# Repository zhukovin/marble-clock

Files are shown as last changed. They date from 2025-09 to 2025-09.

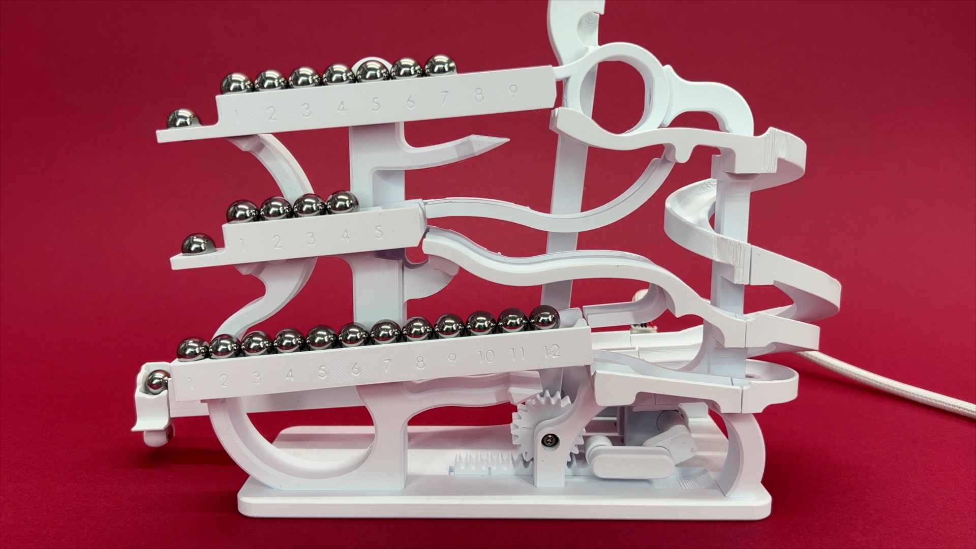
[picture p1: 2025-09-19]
Pictures/How To Assemble the See Saw Clock.jpg

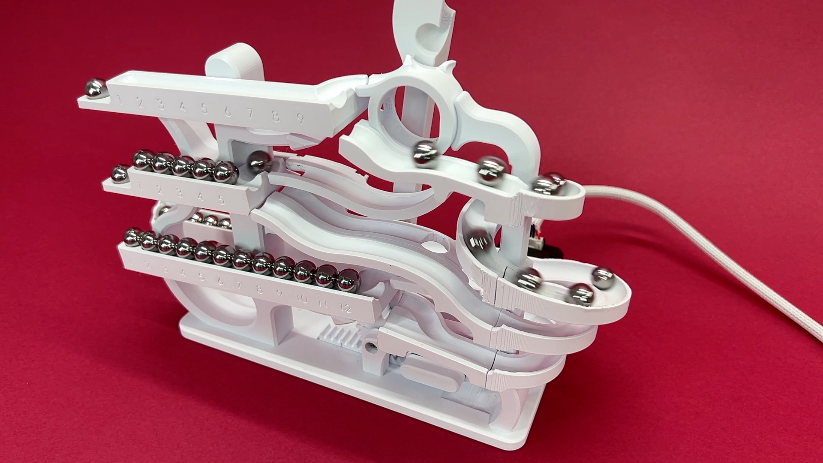
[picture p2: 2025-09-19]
Pictures/How To Assemble the See Saw Clock 4.jpg

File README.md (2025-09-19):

# marble-clock

https://engineezy.com/products/the-tipping-marble-clock

1. 11 3x10x4 bearings: https://a.co/d/4JFZjME
1. M3 Screw Kit: https://a.co/d/3sWPaf0
1. 32 0.5in ball bearings: https://a.co/d/eDzJ6P2
1. Nema 17 Motor: https://a.co/d/04mfYYL
1. 1 GT2 Pulley: https://a.co/d/fuRD2cA
1. A4988 Stepper Motor Driver: https://a.co/d/fOQgJpc
1. Wemos d1 mini ESP8266: https://a.co/d/8dCLFfo
1. Silicone grease: https://a.co/d/iCrpBB1

https://www.youtube.com/watch?v=GmLEBhJY5ks

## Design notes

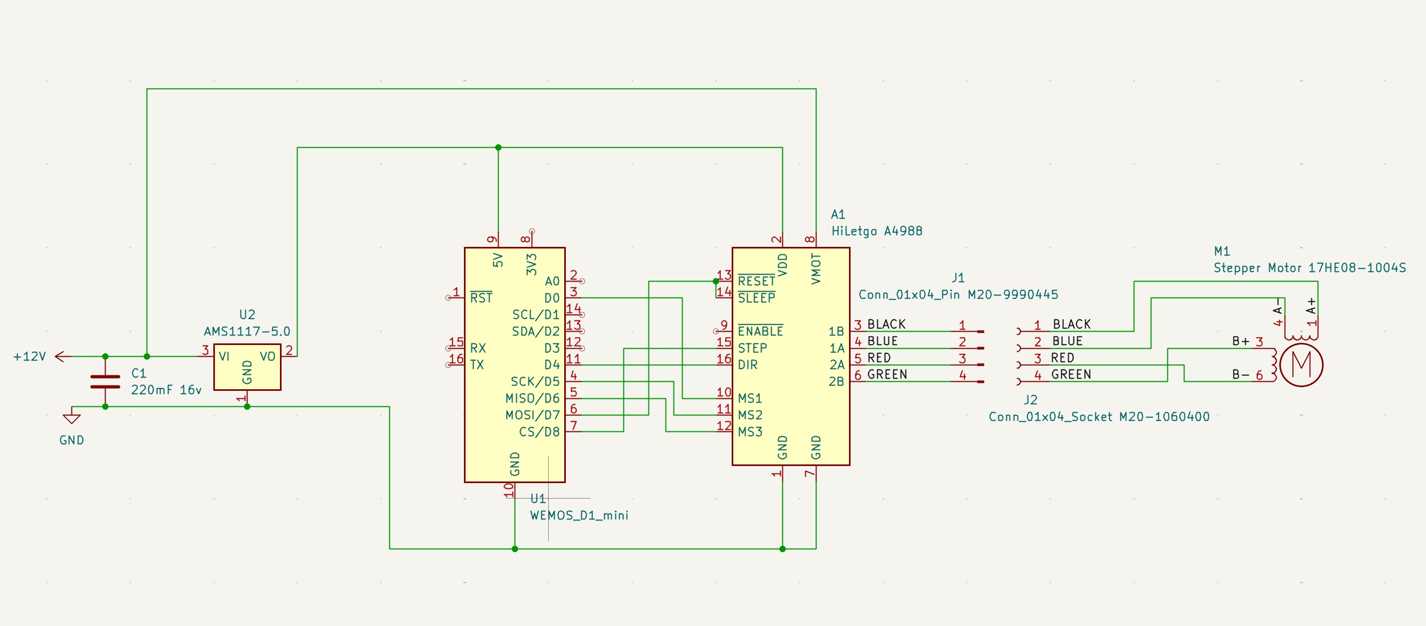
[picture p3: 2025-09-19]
schematic.jpg

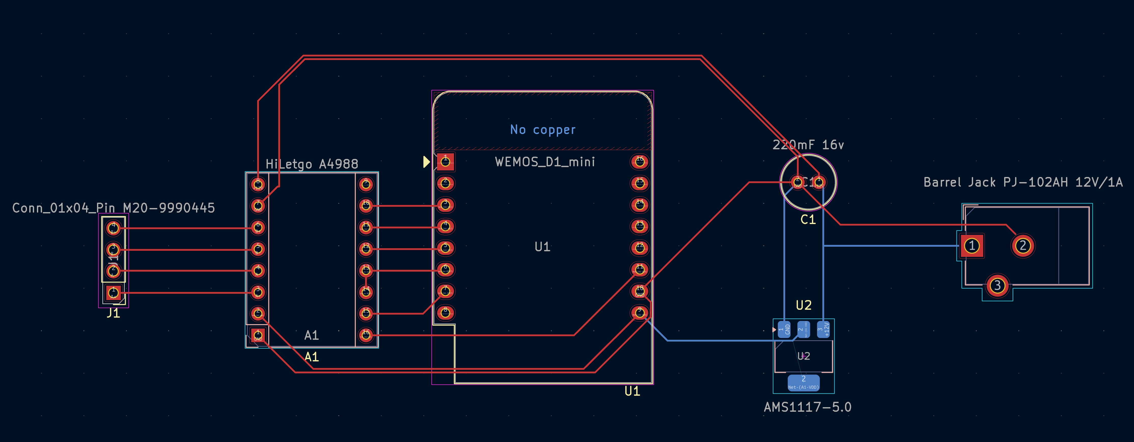
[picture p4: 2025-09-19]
pcb.jpg

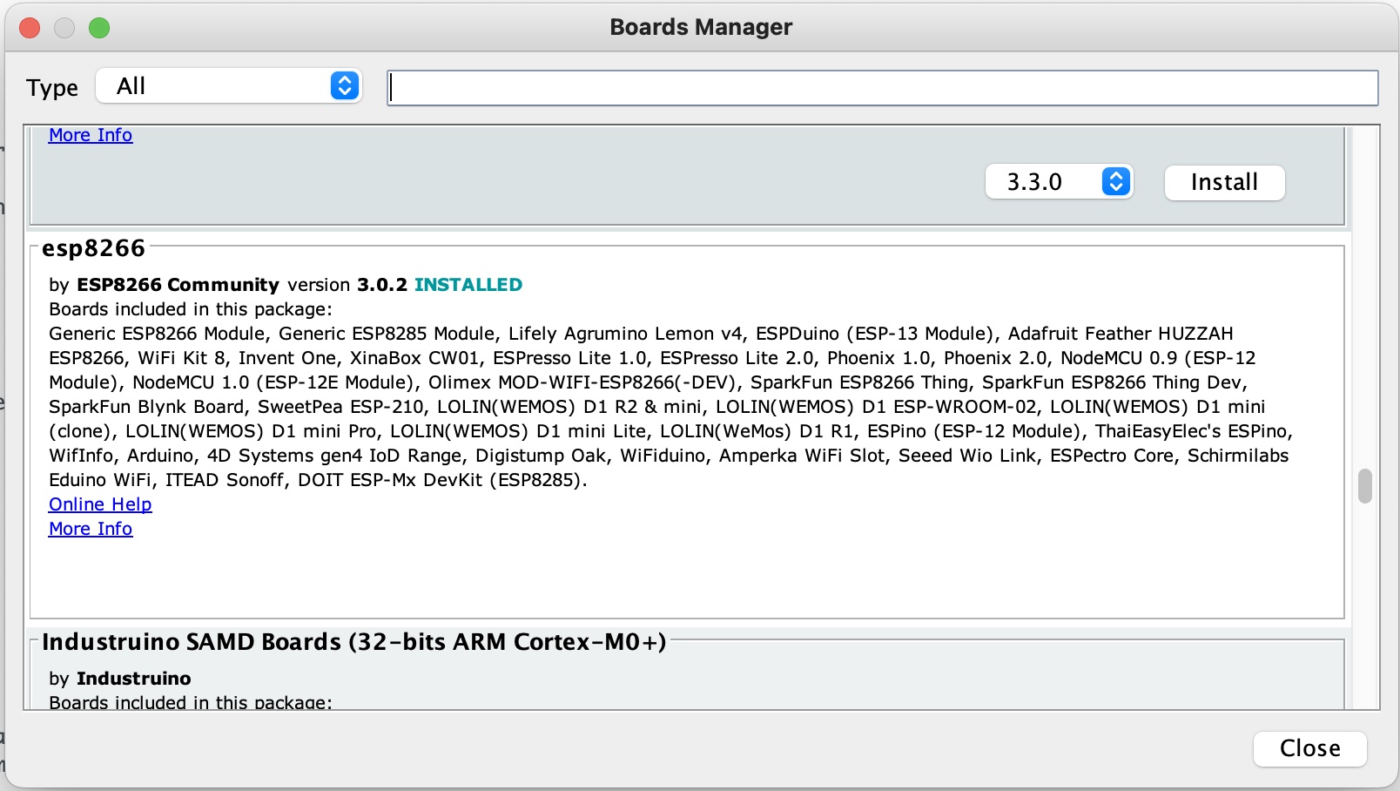
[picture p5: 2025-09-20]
Arduino/Wemos-esp8266-board.jpg

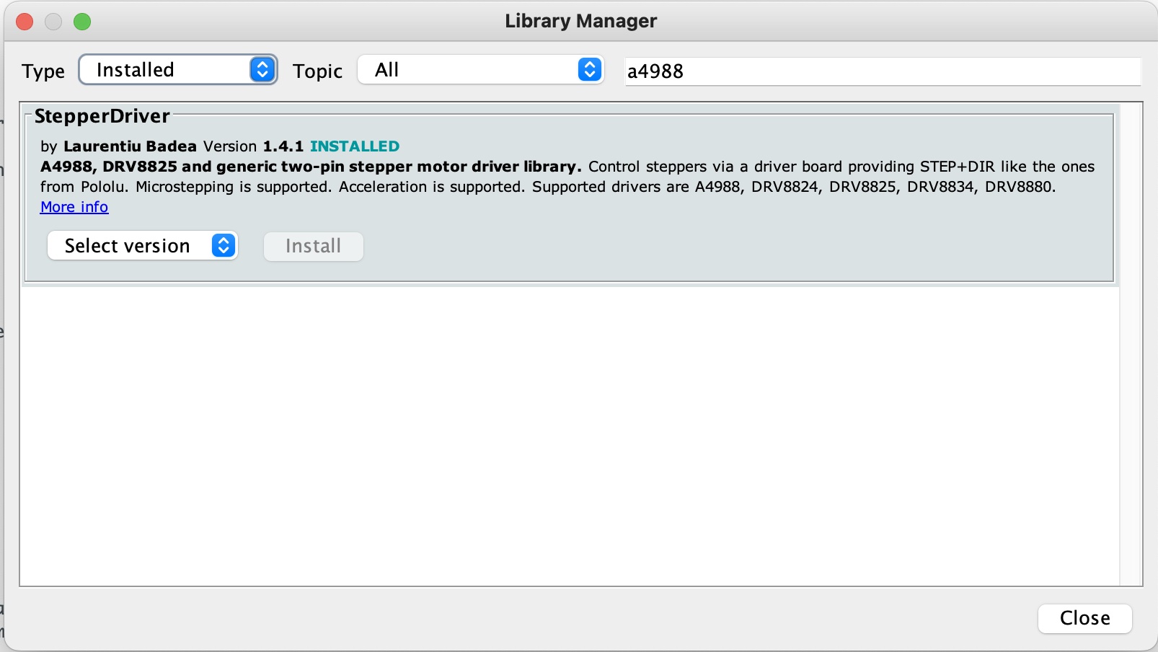
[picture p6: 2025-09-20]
Arduino/A4988-library.jpg

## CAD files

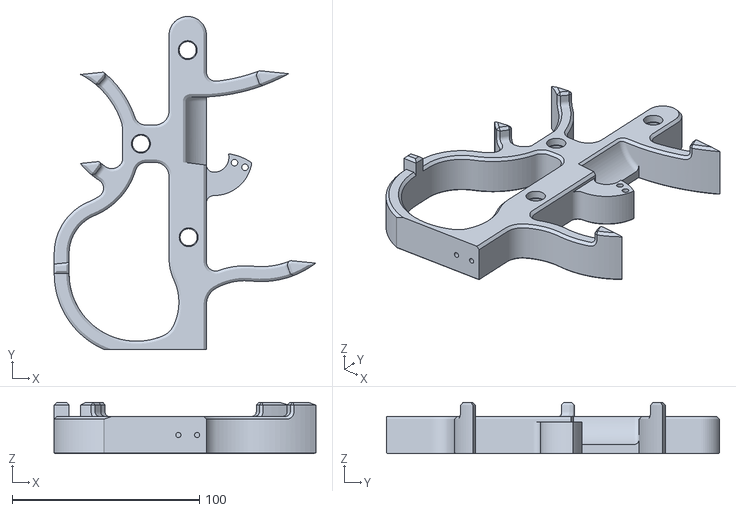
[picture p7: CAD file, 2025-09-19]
Printed/Main Post.stl
139.8 x 178.0 x 27.5

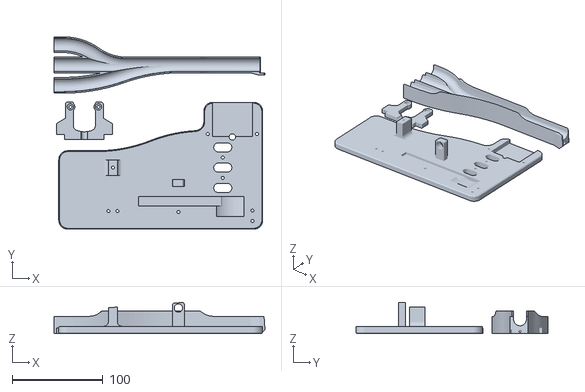
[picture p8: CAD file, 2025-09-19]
Part Layouts/Build 2 - Base Components.stl
232.7 x 212.3 x 34.2

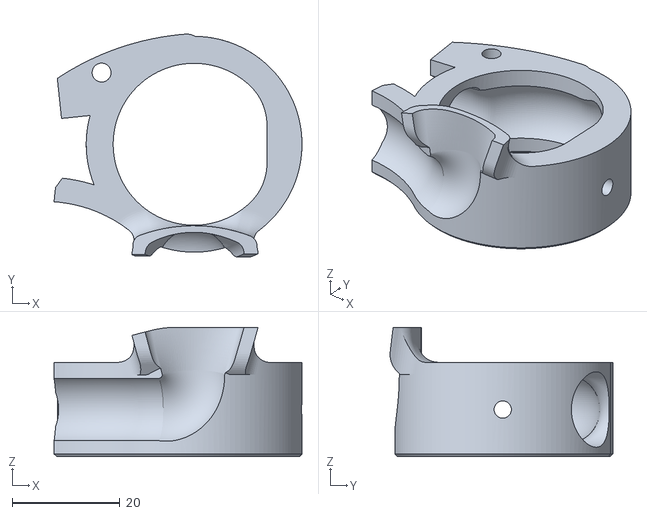
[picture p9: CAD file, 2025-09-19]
Printed/modification/Catcher Circle.stl
46.0 x 41.3 x 24.0

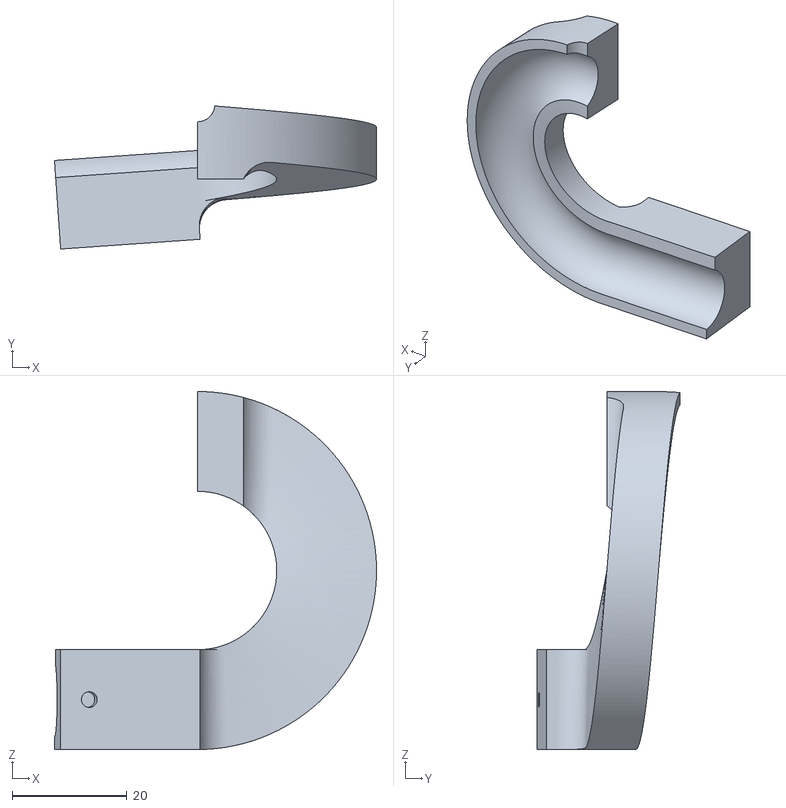
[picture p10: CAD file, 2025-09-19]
Printed/Track Segment Lower-Helix (Needs Support).stl
56.1 x 24.9 x 62.4

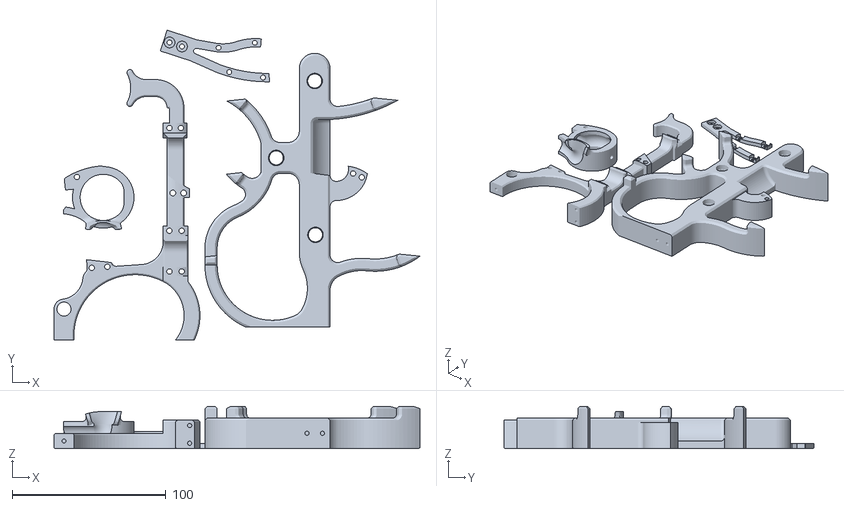
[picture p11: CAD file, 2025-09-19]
Part Layouts/Build 3 - Mounting Posts.stl
237.9 x 201.3 x 27.5

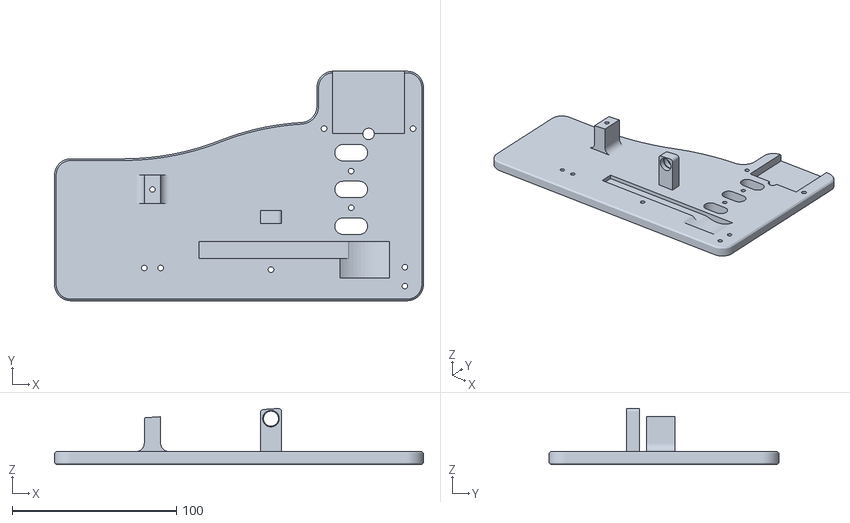
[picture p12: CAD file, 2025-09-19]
Printed/Base Plate.stl
225.0 x 140.0 x 34.2

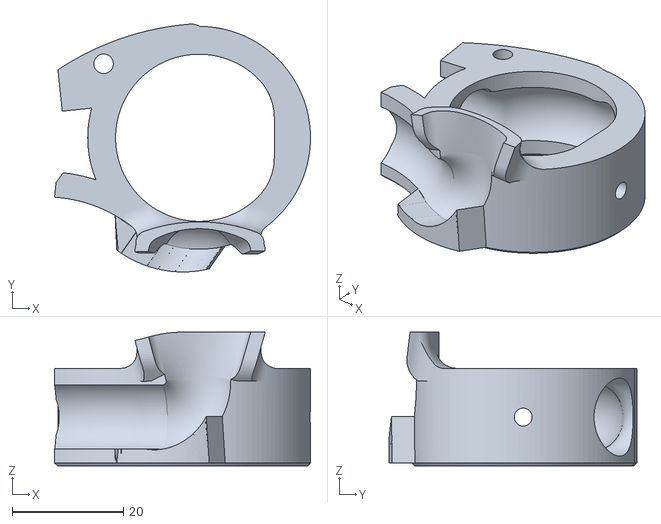
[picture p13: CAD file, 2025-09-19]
Printed/modification/Clock-circlee-guarded.stl
46.0 x 44.5 x 24.0

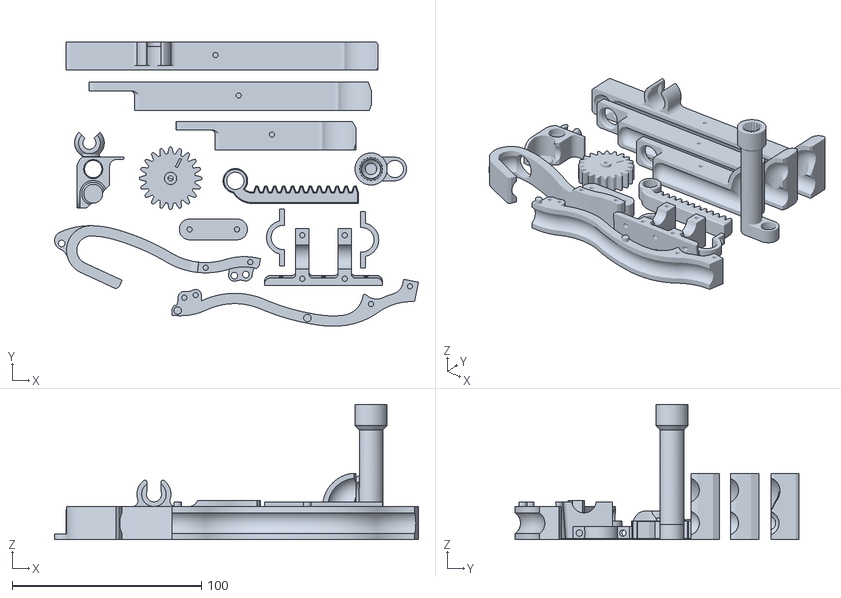
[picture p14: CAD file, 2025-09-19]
Part Layouts/Build 1 - Small Parts.stl
192.2 x 150.2 x 71.5

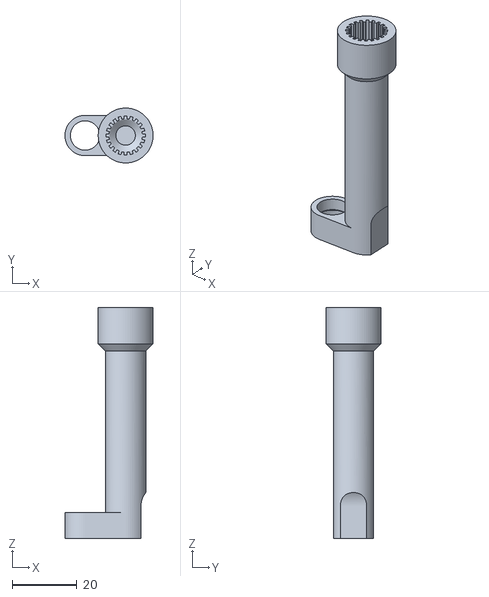
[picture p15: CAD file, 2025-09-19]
Printed/Shaft.stl
27.3 x 17.0 x 71.5

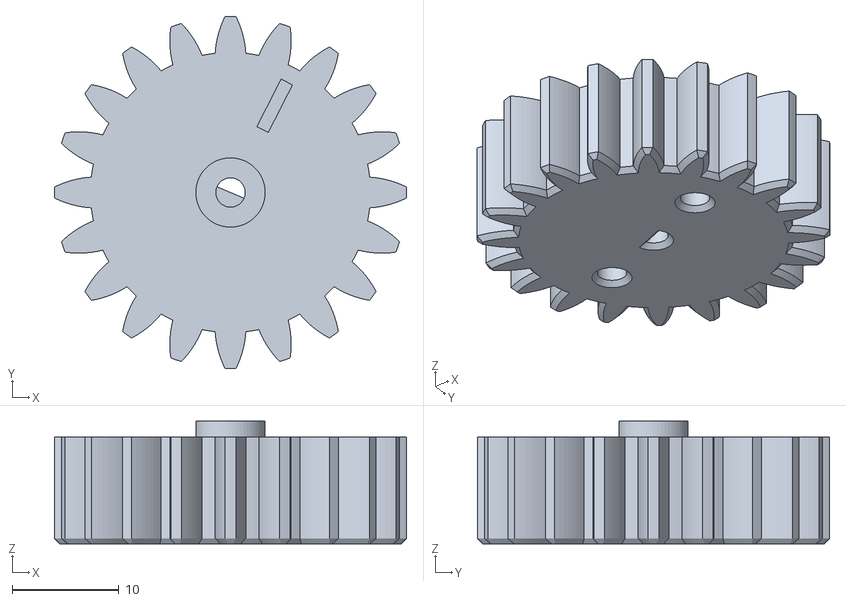
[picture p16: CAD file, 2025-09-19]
Printed/Gear for Arm.stl
33.0 x 33.0 x 11.5

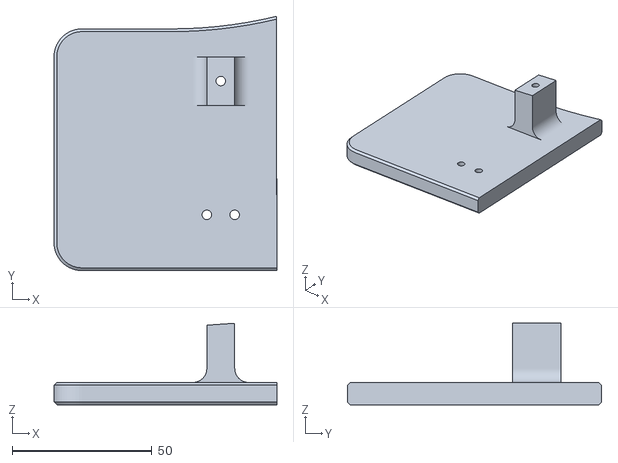
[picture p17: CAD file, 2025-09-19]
Printed/Base Plate 1.stl
79.9 x 91.1 x 29.2

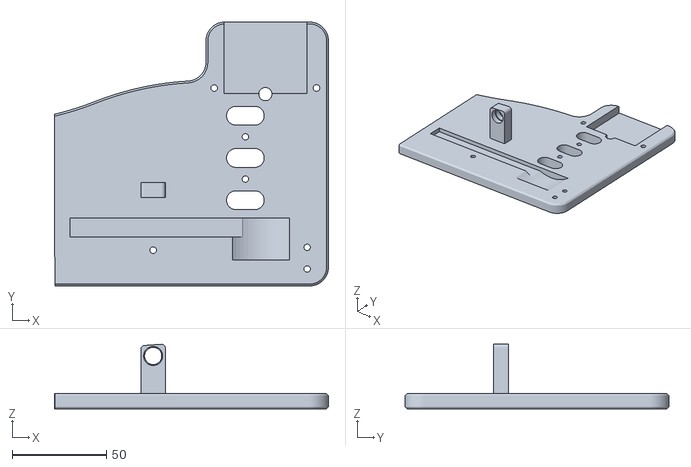
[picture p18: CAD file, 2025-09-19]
Printed/Base Plate 2.stl
145.3 x 140.0 x 34.2

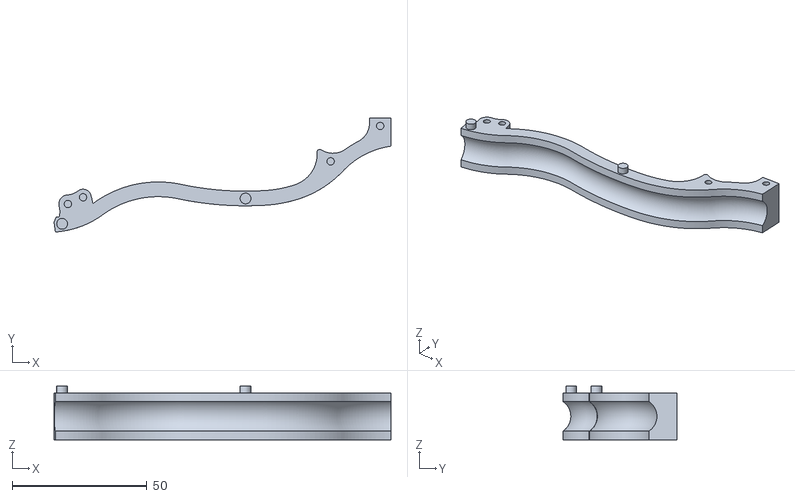
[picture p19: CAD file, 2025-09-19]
Printed/Track Segment Middle-Front.stl
124.9 x 42.4 x 19.9

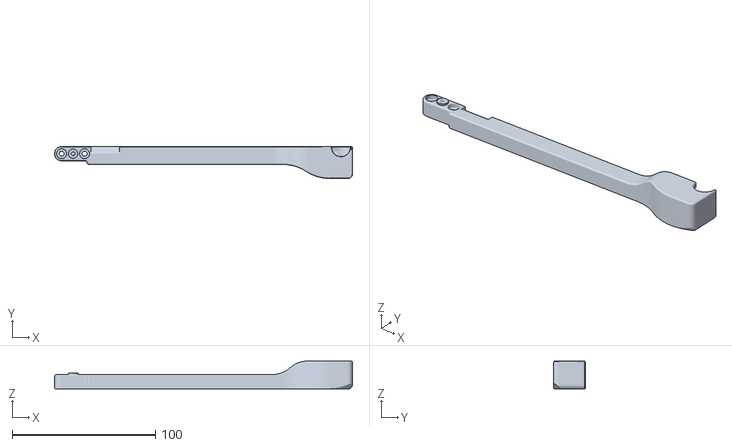
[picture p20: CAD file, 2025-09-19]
Printed/Lift Arm (Needs Support).stl
208.0 x 22.2 x 19.5

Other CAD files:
Printed/Shaft Mount.stl
Printed/Single Minutes Pivot.stl
Printed/Track Segment Top-Helix-2 (Needs Support).stl
Printed/Crank Link.stl
Printed/Accumulator.stl
Printed/Back Track Mount.stl
Printed/Ball Distributor.stl
Printed/Hours Arm Pivot.stl
Printed/Motor Mount.stl
Printed/Rack.stl
Printed/Side Post.stl
Printed/Tens Minutes Pivot.stl
Printed/Track Segment Lower (Needs Support).stl
Printed/Track Segment Middle-Back.stl
Printed/Track Segment Middle-Helix (Needs Support).stl
Printed/Track Segment Top-Back (Needs Support).stl
Printed/Track Segment Top-Helix (Needs Support).stl

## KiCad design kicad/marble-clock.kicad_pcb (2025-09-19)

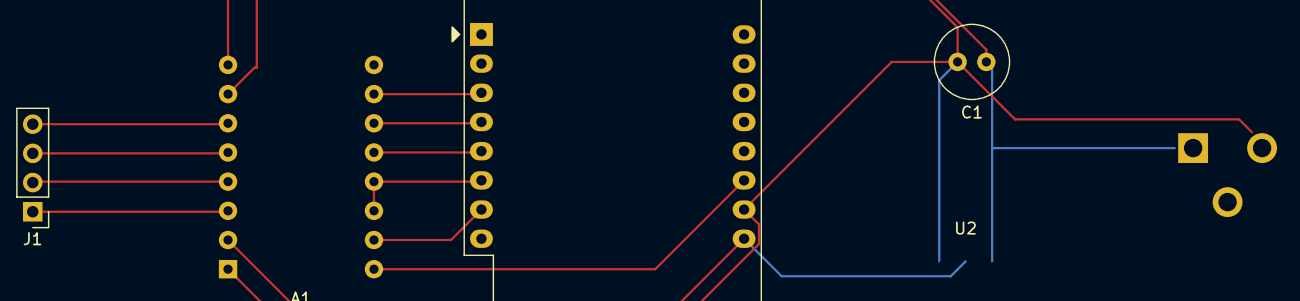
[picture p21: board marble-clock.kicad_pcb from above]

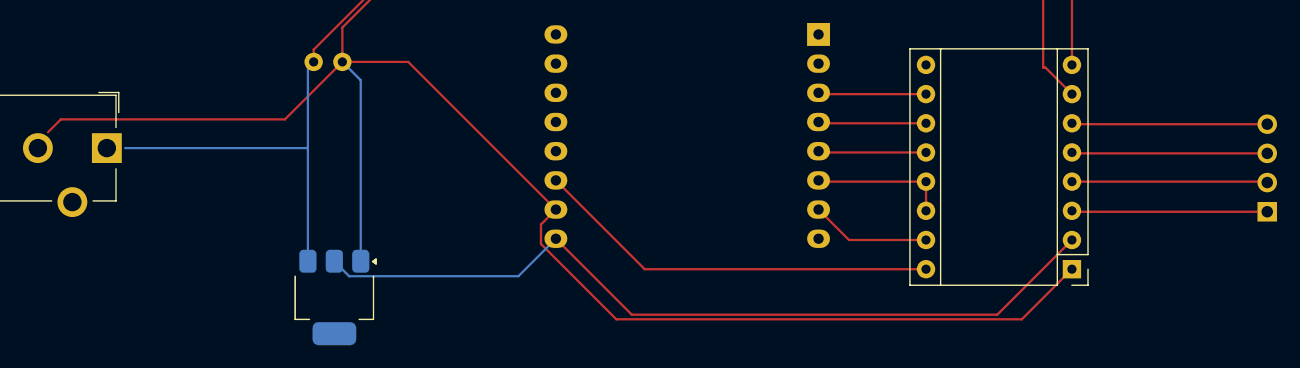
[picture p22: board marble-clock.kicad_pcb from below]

Board: 2 copper layers, 5 parts (2 on the bottom side), 13 nets.

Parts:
A1: HiLetgo A4988; Pololu_Breakout-16_15.2x20.3mm
C1: 220mF 16v; C_Radial_D6.3mm_H11.0mm_P2.50mm
J1: Conn_01x04_Pin M20-9990445; PinHeader_1x04_P2.54mm_Vertical
U1: WEMOS_D1_mini; WEMOS_D1_mini_light
U2: AMS1117-5.0; SOT-223-3_TabPin2

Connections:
+12V: A1.8 (VMOT), C1.1, U2.3 (VI)
/A+: A1.3 (1B), J1.1
/A-: A1.4 (1A), J1.2
/B+: A1.6 (2B), J1.4
/B-: A1.5 (2A), J1.3
GND: A1.1 (GND), A1.7 (GND), C1.2, U1.10 (GND), U2.1 (GND)
unnamed: A1.16 (DIR), U1.11 (D4)
unnamed: A1.10 (MS1), U1.3 (D0)
unnamed: A1.11 (MS2), U1.4 (SCK/D5)
unnamed: A1.12 (MS3), U1.5 (MISO/D6)
unnamed: A1.15 (STEP), U1.7 (CS/D8)
unnamed: A1.2 (VDD), U1.9 (5V), U2.2 (VO)
unnamed: A1.13 (~RESET), A1.14 (~SLEEP), U1.6 (MOSI/D7)

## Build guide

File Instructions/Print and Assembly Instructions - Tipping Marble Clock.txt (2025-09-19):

Thanks so much for downloading this model!

All you have to do is import the files from the main folder into your slicer, arrange, and hit print. 

Some Parts need supports! They are labeled in the filename.

This video shows you how to assemble the model: https://youtu.be/GmLEBhJY5ks

If you have any questions or need any help while printing or assembling this piece, 
please do not hesitate to reach out to me at jbvcreative@gmail.com

You will need the following additional components to assemble this clock:

11 3x10x4 bearings: https://geni.us/ytgU1tC
M3 Screw Kit https://geni.us/CnX30
32 0.5in ball bearings: https://geni.us/uLEbw
Nema 17 Motor https://geni.us/IbL6D0
1 GT2 Pulley https://geni.us/l3MG

You will also need a way to drive the Stepper Motor:

I recommend this board: https://geni.us/2sH7WYY
Real Time Module (Optional): https://geni.us/rtKYLJT

(Here is a really good tutorial for driving clocks with a stepper motor: https://www.youtube.com/watch?v=PR4PXR7RXEY&amp;t=253s)

--Recommended print settings--
PLA Material
0.4mm nozzle
0.2mm layer height
15%-18% infill

**This model was specifically designed for this material and print settings - I can't 
guarantee it will work with other materials.  Feel free to email me if you have any questions

If you would like to further support my channel, I would hugely appreciate it! To do so, you can subscribe to my youtube channel, follow me on instagram, or become a patreon member. Links are below:

www.instagram.com/engineezy_
www.youtube.com/@engineezy
www.patreon.com/engineezy

Disclaimer: These files are for personal use only and cannot be copied or sold. If you would like to sell printed versions of this file, you can do so by subscribing to a license through my patreon- patreon.com/jbvcreative 
If you have any questions, feel free to reach out.

©Engineezy

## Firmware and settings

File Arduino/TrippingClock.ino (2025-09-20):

#include <Arduino.h>
#include "A4988.h"

// The pin mapping is for D1 mini ESP8266
// Dx --> GPIOxx
#define D0 16
#define D1 5
#define D2 4
#define D3 0
#define D4 2
#define D5 14
#define D6 12
#define D7 13
#define D8 15



int Step = D8; //GPIO14---D5 of Nodemcu--Step of stepper motor driver
int Dire  = D4; //GPIO2---D4 of Nodemcu--Direction of stepper motor driver
int Sleep = D7; //GPIO12---D6 of Nodemcu-Control Sleep Mode on A4988
int MS1 = D0; //GPIO13---D7 of Nodemcu--MS1 for A4988
int MS2 = D5; //GPIO16---D0 of Nodemcu--MS2 for A4988
int MS3 = D6; //GPIO15---D8 of Nodemcu--MS3 for A4988

//Motor Specs
const int spr = 200; //Steps per revolution
int RPM = 8; //Motor Speed in revolutions per minute - Here we set the RPM to 1 rpm to match the speed of second hand from a clock
int Microsteps = 16; //Stepsize (1 for full steps, 2 for half steps, 4 for quarter steps, etc)

//Providing parameters for motor control
A4988 stepper(spr, Dire, Step, MS1, MS2, MS3);

unsigned long loopStart;

void setup() {
  Serial.begin(9600);
  pinMode(Step, OUTPUT); //Step pin as output
  pinMode(Dire,  OUTPUT); //Direcction pin as output
  pinMode(Sleep,  OUTPUT); //Set Sleep OUTPUT Control button as output
  digitalWrite(Step, LOW); // Currently no stepper motor movement
  digitalWrite(Dire, LOW);
  
  // Set target motor RPM to and microstepping setting
  stepper.begin(RPM, Microsteps);
}

void loop() {
    loopStart = millis();

    digitalWrite(Sleep, HIGH); //A logic high allows normal operation of the A4988 by removing from sleep
    stepper.rotate(360);
    digitalWrite(Sleep, LOW);

    unsigned long elapsed = millis() - loopStart;
    unsigned long remaining = 60000UL > elapsed ? 60000UL - elapsed : 0;

    // Sleep in chunks (watchdog only allows up to ~8s)
    while (remaining > 0) {
      wdt_reset();  // prevent watchdog reset
      unsigned long sleepMs = remaining > 8000 ? 8000 : remaining;
      delay(sleepMs);
      remaining -= sleepMs;
    }
}

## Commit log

2025-09-19 Initial version
    [Accumulator.stl, Back Track Mount.stl, Ball Distributor.stl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]
2025-09-19 Add BOM and links
2025-09-19 Add motor data sheet
2025-09-19 Add PCB photos
2025-09-20 Add Arduino code
